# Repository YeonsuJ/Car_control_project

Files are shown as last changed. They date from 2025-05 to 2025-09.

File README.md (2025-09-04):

# 핸들링 모션 기반 RC카 네트워크 시스템 개발
이 리포지토리는 `핸들링 모션 기반 RC카 네트워크 시스템` 프로젝트의 기획부터 최종 구현까지 모든 개발 과정, 소스 코드, 기술 문서를 기록하는 메인 개발 아카이브입니다.

## 프로젝트 문서
프로젝트 개발 과정에서 작성된 모든 문서는 develop 브랜치의 `docs` 폴더 내에 체계적으로 정리되어 있습니다.
```
docs/
├── 3d_model/           # 컨트롤러 외형 설계 도면
├── datasheets/         # 개발에 참고한 부품 데이터시트
├── dev_logs/           # 상세 개발 일지
├── images/             # 프로젝트 관련 사진
├── troubleshooting/    # 문제 해결 과정 기록
├── wiring_diagram/     # 하드웨어 배선도
├── dev_log_summary.md  # 주간 개발 일지 요약
└── parts_list.md       # 전체 부품 목록
```
**주간 개발 일지 요약** : 전체 진행 상황은 [dev_log_summary.md](./docs/dev_log_summary.md) 에서 확인하실 수 있습니다.

---

## 브랜치 전략
기능 단위 개발을 위해 아래와 같이 브랜치를 나누어 관리합니다. 각 브랜치에는 해당 기능의 개발 소스 코드가 커밋 단위로 기록되어 있으며, 상세 개발 히스토리는 별도 문서로 확인할 수 있습니다.

- `main` : 최종 안정화 버전의 코드가 병합되는 기본 브랜치 
- `develop` : 개발 과정에서 작성된 모든 문서를 관리하는 브랜치
- `Unit_controller` : 컨트롤러 유닛 개발 → [[상세 히스토리](https://github.com/YeonsuJ/Car_control_project/tree/Unit_controller/ver_Unit_controller.md)]
- `Unit_car_central` : 차량 메인 제어 유닛 개발 → [[상세 히스토리](https://github.com/YeonsuJ/Car_control_project/tree/Unit_car_central/ver_Unit_car_central.md)]
- `Unit_car_sensor` : 차량 센서 제어 유닛 개발 → [[상세 히스토리](https://github.com/YeonsuJ/Car_control_project/tree/Unit_car_sensor/ver_Unit_car_sensor.md)]
- `Unit_car_status` : 차량 상태 디스플레이 유닛 개발 → [[상세 히스토리](https://github.com/YeonsuJ/Car_control_project/tree/Unit_car_status/ver_Unit_car_status.md)]

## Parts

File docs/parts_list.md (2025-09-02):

# 개발 간 사용한 보드 및 모듈

**Board**
| 품목 | 용도 | 수량 | 이미지 |
| :---: | :---: |:---: |:---: |
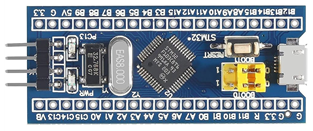
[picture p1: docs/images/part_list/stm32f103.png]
| STM32F103C8T6 | controller MCU <br> car_central ECU <br> car_status ECU <br> car_sensor ECU |4| |
<br/>

**Sensor**
| 품목 | 용도 | 수량 | 이미지 |
| :---: | :---: |:---: |:---: |
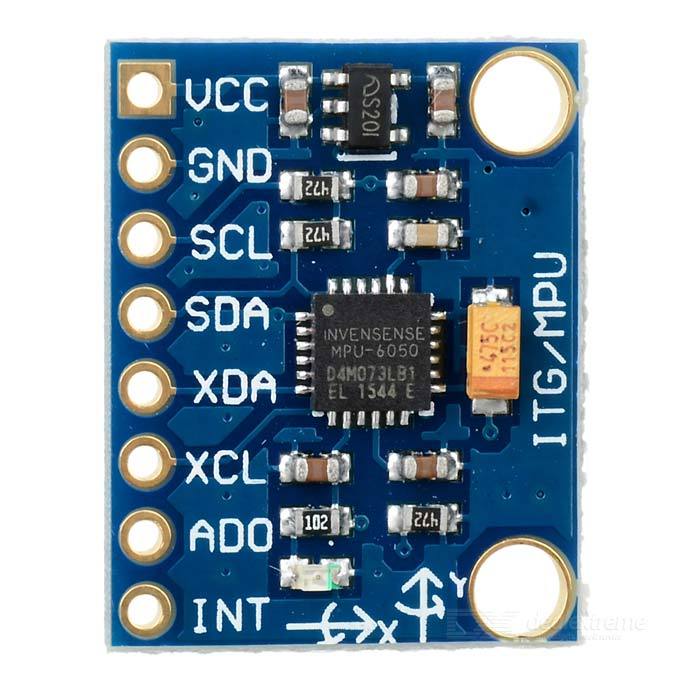
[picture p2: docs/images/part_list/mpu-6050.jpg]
| [MPU-6050] 6축 IMU 센서 | controller - 모션 제어|1||
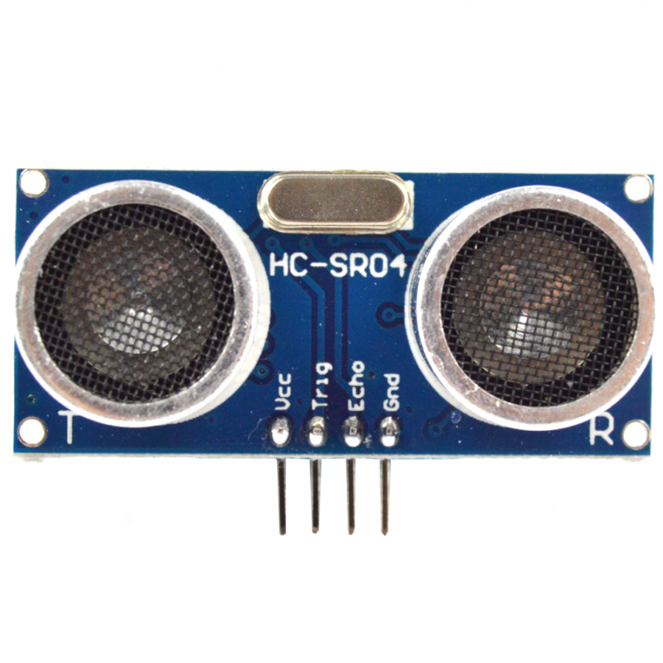
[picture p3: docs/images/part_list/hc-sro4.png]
|[HC-SRO4] 초음파센서|전/후방 장애물 감지|2||
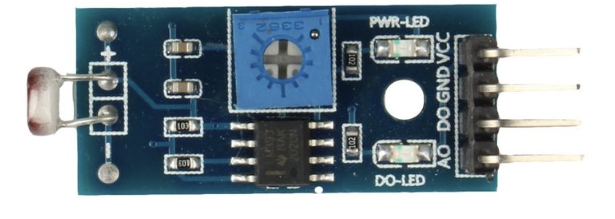
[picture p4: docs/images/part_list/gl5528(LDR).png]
|[LM393 ldr] 조도센서|주변 밝기 판단|1||
<br/>

**Communication module**
| 품목 | 용도 | 수량 | 이미지 |
| :---: | :---: |:---: |:---: |
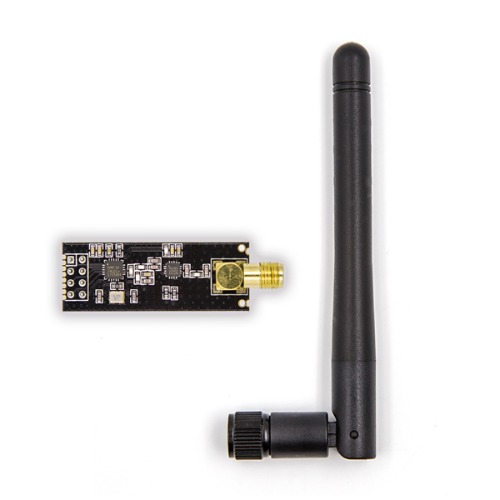
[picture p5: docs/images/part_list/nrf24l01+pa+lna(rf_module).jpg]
|[NRF24L01+PA+LNA] 2.4G 무선 모듈|car-controller RF 통신|2||
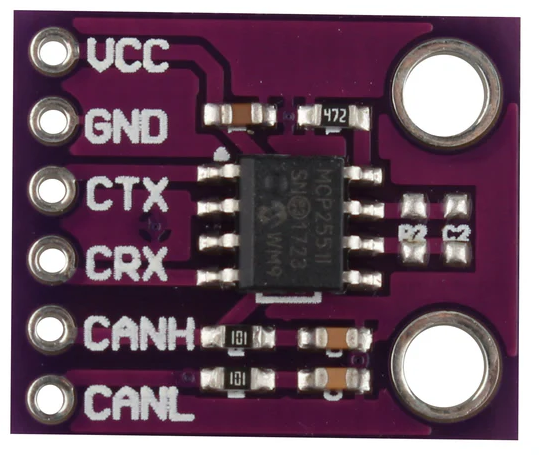
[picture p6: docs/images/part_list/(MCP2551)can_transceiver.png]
|[MCP2551] CAN 트랜시버 모듈| car - can 통신 |3||
<br/>

**Motor**
| 품목 | 용도 | 수량 | 이미지 |
| :---: | :---: |:---: |:---: |
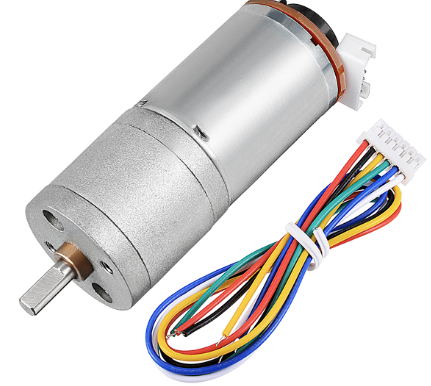
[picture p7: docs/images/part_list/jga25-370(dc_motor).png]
|[JGA25-370] DC모터|내부 인코더를 통해 dc모터의 RPM 확인가능|1||
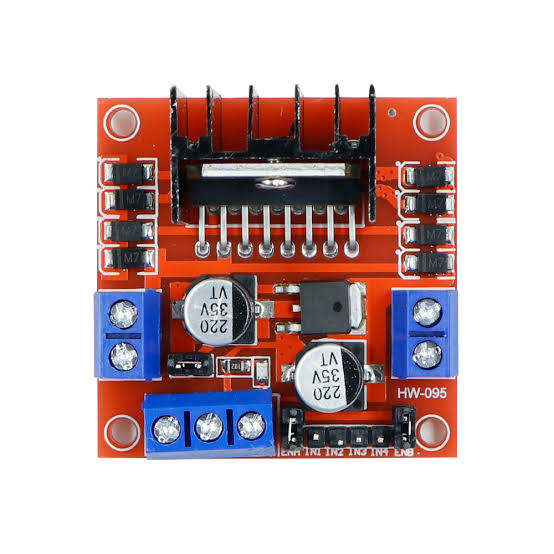
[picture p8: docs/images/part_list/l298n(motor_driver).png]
|L298N|Dc motor driver - DC모터 PWM 제어 및 방향 변경|1||
|진동모터|controller - 충돌 경고 핸들 진동|2|부품 이미지|
|[MG996R]servo 모터|전륜 조향|1|부품 이미지|
<br/>

**Etc**
| 품목 | 용도 | 수량 | 이미지 |
| :---: | :---: |:---: |:---: |
|RC카 섀시, 휠|차량의 뼈대|1|부품 이미지|
|Locker 스위치| car - 배터리 on/off |1|부품 이미지|
|토글 스위치| controller - 기어변속|1|부품 이미지|
|tactile 스위치|브레이크,악셀 버튼용|2|부품 이미지|
|LED|전조등, 후미등, 브레이크등|6|부품 이미지|
|OLED 디스플레이| controller - 주행 중 현황 확인 <br> car - 차량 상태 확인 |2|부품 이미지|
|충전형 18650 리튬 배터리(3000mAh)| car - 3s <br> controller - 2S|5|부품 이미지|
|DC 스텝다운 컨버터| MCU 5V 전압공급 목적 강압 <br> car : 12v->5v <br> controller : 8v->5v |2|부품 이미지|
|저항|120옴 - CAN 종단저항(3) <br> 100옴 - LED용(6)|9|부품 이미지|

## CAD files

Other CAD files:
docs/3d_model/Cap.ipt
docs/3d_model/Steering_Wheel.ipt

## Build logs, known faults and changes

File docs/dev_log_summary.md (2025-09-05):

# Weekly Dev_log Summary 

## 1주차 (25-05-12 ~ 25-05-18) 
|내용|문서 링크|커밋해시|
|---|:---:|:---:|
|- 초기 아이디어 구상<br>- 보드 및 부품 선정 후 구매<br>- 마일드스톤 개괄 작성|[Initial_Planning.md](./dev_logs/Initial_Planning.md)|-|

---

## 2주차 (25-05-19 ~ 25-05-25)
|내용|문서 링크|커밋해시|
|---|:---:|:---:|
|Git commands 학습|[Github_Manuals.md](./dev_logs/Github_Manuals.md)|-|
|Github을 활용한 버전관리법 학습|[Managing_Ver.md](./dev_logs/Managing_Ver.md)|-|
|STM32CubeIDE와 Git & Github 관리/연동|[Managing_Git_CubeIDE.md](./dev_logs/Managing_Git_CubeIDE.md)|-|
|폴링방식 기반 -> 인터럽트 기반 타이머 인풋 캡쳐 활용 초음파센서 거리값 출력 로직 구현 |[Ultrasonic.md](./dev_logs/Ultrasonic.md)|[`7165ee7`](https://github.com/YeonsuJ/Car_control_project/commit/7165ee7f55b6ba93f8e09380047e063f922466cb)|

---

## 3주차 (25-05-26 ~ 25-06-01)
|내용|문서 링크|커밋해시|
|---|:---:|:---:|
|자이로센싱값 -> OLED 모니터링 로직 구현|[Gyro_Display.md](./dev_logs/Gyro_Display.md)|[`229aaa8`](https://github.com/YeonsuJ/Car_control_project/commit/229aaa8b4e313b1294b8de80c3d619d1e4bc61c4)|
|배터리 잔량 측정 -> LCD 모니터링 로직 구현|[Lcd_Battery_Check.md](./dev_logs/Lcd_Battery_Check.md)|[`3cadc21`](https://github.com/YeonsuJ/Car_control_project/commit/3cadc214babbb125b15034e2ebce0408e0c439cd)|
|서보모터 PWM 듀티비 기반 조향 각도 매핑 및 좌/우 조향 한계각 보정|[Servo_Motor.md](./dev_logs/Servo_Motor.md)|[`1d18eda`](https://github.com/YeonsuJ/Car_control_project/commit/1d18eda88c05c9aac707a6153e64591776d5ae05)|
|자이로 roll 값 -> 서보모터 구동|[Gyro_Pwm_Mapping.md](./dev_logs/Gyro_Pwm_Mapping.md)|[`7dc0c12`](https://github.com/YeonsuJ/Car_control_project/commit/7dc0c1298043c86b4969e85140554ca7ac16d90a)|

---

## 4주차 (25-06-02 ~ 25-06-08)
|내용|문서 링크|커밋해시|
|---|:---:|:---:|
|버튼 눌림 시간 측정 로직 구현|[Timer_Switch.md](./dev_logs/Timer_Switch.md)|[`7dcde54`](https://github.com/YeonsuJ/Car_control_project/commit/7dcde5411003d99339164ecea6fa701451369387)|
|PWM 듀티비 기반 DC모터 동작 로직 구현|[Dc_Motor.md](./dev_logs/Dc_Motor.md)|[`45c4e16`](https://github.com/YeonsuJ/Car_control_project/commit/45c4e164ce43241788da8687f2dbf96ccc241a7f)|

---

## 5주차 (25-06-09 ~ 25-06-15)
|내용|문서 링크|커밋해시|
|---|:---:|:---:|
|버튼 누름 시간 기반 DC 모터 속도 제어 및 로커 스위치 전/후진 전환 + OLED 상태 표시 기능 구현|-|[`ad9f4bc`](https://github.com/YeonsuJ/Car_control_project/commit/ad9f4bc341844dbb1dcecefefb23643b87a2f076)|
|초음파센서 거리설정값 기반 진동모터 햅틱 피드백 로직 추가|[Ultrasonic_Vibration.md](./dev_logs/Ultrasonic_Vibration.md)|[`3be3675`](https://github.com/YeonsuJ/Car_control_project/commit/3be3675e9acbf0c19c06f436050e4edda30a9942)|

---

## 6주차 (25-06-16 ~ 25-06-22)
|내용|문서 링크|커밋해시|
|---|:---:|:---:|
|선형 보간 방식 기반 ADC 배터리 측정 후 OLED 출력 로직으로 수정|[Adc_Oled_Battery_Check.md](./dev_logs/Adc_Oled_Battery_Check.md)|[`7bd584e`](https://github.com/YeonsuJ/Car_control_project/commit/7bd584ef51410f1fcd1aae941d038a377702ed81)|
|핸들 디자인·3D 모델링 및 출력|[Controller_3D_Modeling_Log.md](./dev_logs/Controller_3D_Modeling_Log.md)|모델링 파일 : [Cap.ipt](../3d_model/Cap.ipt) / [Steering_Wheel.ipt](../3d_model/Steering_Wheel.ipt)|

---

## 7주차 (25-06-23 ~ 25-06-29)
|내용|문서 링크|커밋해시|
|---|:---:|:---:|
|DC모터와 Servo모터 동작 기능 통합 및 핀 라벨링 추가|-|[`b474df6`](https://github.com/YeonsuJ/Car_control_project/commit/b474df67b9a24d75a08725cf00dbaa94170cabac)|
|RF 통신을 통한 roll 값, 악셀 / 브레이크 버튼 눌림 시간 송수신 및 실시간 서보모터 조향 구현 (m3)|[M3_RF_Communication.md](./dev_logs/M3_RF_Communication.md)|[`RX`](https://github.com/YeonsuJ/Car_control_project/commit/cbc18035c71e6f3c50977fd6d9abb157786e36d2) / [`TX`](https://github.com/YeonsuJ/Car_control_project/commit/88aaa169f57b4323f77507a8af936f329d8cdfcc)|

---

## 8주차 (25-06-30 ~ 25-07-06)
|내용|문서 링크|커밋해시|
|---|:---:|:---:|
|CAN 통신 송/수신 초기 기능 구현 (m3)|[Can_Communication.md](./dev_logs/Can_Communication.md)|[`RX`](https://github.com/YeonsuJ/Car_control_project/commit/89800bed5bbd43df382bfc1d63d63a506a9933f4) / [`TX`](https://github.com/YeonsuJ/Car_control_project/commit/e1316b007e2b4ca462092e7ce0a50db136938af6)|
|M3보드 기반 RF 송/수신 모터 제어 통합 (v1.0.0)|[V1.0.0_RF_MotorCtrl.md](./dev_logs/V1.0.0_RF_MotorCtrl.md)|[`central_v1.0.0`](https://github.com/YeonsuJ/Car_control_project/commit/087c00a452b5e8d1e8889b24831789548ee6a3f0) / [`controller_v1.0.0`](https://github.com/YeonsuJ/Car_control_project/commit/de77deb8e3d7acceab46b517a5e457805b62f0cb)|

---

## 9주차 (25-07-07 ~ 25-07-13)
|내용|문서 링크|커밋해시|
|---|:---:|:---:|
|코드 리팩토링 및 Locker 스위치 기반 전/후진 기능 추가, <br>DC모터 Encoder 기반 RPM 측정 로직 추가 (v1.1.0)|[V1.1.0_Locker_Encoder.md](./dev_logs/V1.1.0_Locker_Encoder.md)|[`central_v1.1.0`](https://github.com/YeonsuJ/Car_control_project/commit/94a4a332562ac80192bba8cc971c298cab48cbfd) / [`controller_v1.1.0`](https://github.com/YeonsuJ/Car_control_project/commit/241c4c5877d608a3723825619a0ed84717d12e22)|
|컨트롤러부 Lokcer -> 토글스위치 기반 전/후진 기어변속 수정 및 센서부 엔코더 기반 RPM 측정 로직 수정|[RPM_Measuring_Dir_Toggle.md](./dev_logs/RPM_Measuring_Dir_Toggle.md)|-|

---

## 10주차 (25-07-14 ~ 25-07-20)
|내용|문서 링크|커밋해시|
|---|:---:|:---:|
|ACK 페이로드 기반 RF 양방향 송수신 구현(v1.5.0)|[V1.5.0_ACK_Payload.md](./dev_logs/V1.5.0_ACK_Payload.md)|[`controller_v1.5.0`](https://github.com/YeonsuJ/Car_control_project/commit/0745e3354e6c7a4ae12c31953c2b0a166a373d1a) / [`central_v1.5.0`](https://github.com/YeonsuJ/Car_control_project/commit/fb063337c0dd13055ecf7afc8d4cca3d3b347613)|
|Broadcast 기반 CAN 송/수신 초음파센서 -> 햅틱센서 제어 통합(v1.5.0)|[V1.5.0_Broadcast_Can_Comm.md](./dev_logs/V1.5.0_Broadcast_Can_Comm.md)|[`central_v1.5.0`](https://github.com/YeonsuJ/Car_control_project/commit/fb063337c0dd13055ecf7afc8d4cca3d3b347613) / [`sensor_v1.5.0`](https://github.com/YeonsuJ/Car_control_project/commit/13f38c18cb6364108f1dbb893375f56113965320) / [`status_v1.5.0`](https://github.com/YeonsuJ/Car_control_project/commit/d7810ab06a289a489a91285c02ddfea00daa1e14)|

---

## 11주차 (25-07-21 ~ 25-07-27)
|내용|문서 링크|커밋해시|
|---|:---:|:---:|
|Controller 부 파일 분할 및 코드 최적화|[V1.6.0_Controller_Refactor.md](./dev_logs/V1.6.0_Controller_Refactor.md)|[`controller_v1.6.0`](https://github.com/YeonsuJ/Car_control_project/commit/033420c3bb7774f772402cf7f1a2d00c62ac3682)|
|Central 부 파일 분할 및 코드 최적화 + CAN 개선|[V1.6.0_Central_Refactor.md](./dev_logs/V1.6.0_Central_Refactor.md)|[`central_v1.6.0`](https://github.com/YeonsuJ/Car_control_project/commit/f1f14c615f58d526c636ad07ba73be2855ed3e86)|
|Sensor 부 파일 분할 및 코드 최적화 + CAN 개선|[V1.6.0_Sensor_Refactor.md](./dev_logs/V1.6.0_Sensor_Refactor.md)|[`sensor_v1.6.0`](https://github.com/YeonsuJ/Car_control_project/commit/22e10d68004d4dc19ce922d08332d6f769065621)|
|Status 부 파일 분할 및 코드 최적화 + CAN 개선, ADC 배터리 측정 추가|[V1.6.0_Status_Refactor.md](./dev_logs/V1.6.0_Status_Refactor.md)|[`status_v1.6.0`](https://github.com/YeonsuJ/Car_control_project/commit/ff784f4d59c5a10102964285e873eb8930eb3fa3)|

---

## 12주차 (25-07-28 ~ 25-08-03)
|내용|문서 링크|커밋해시|
|---|:---:|:---:|
|LDR 기반 전/후진 및 브레이크 상태에 따라 전조등·후미등 제어 로직 추가|[V1.7.0_LDR_Brk_Dir_LED_Ctrl.md](./dev_logs/V1.7.0_LDR_Brk_Dir_LED_Ctrl.md)|[`central_v1.7.0`](https://github.com/YeonsuJ/Car_control_project/commit/c3081ab3b98114f977e82bb3962f7fc1301cce8b) / [`sensor_v1.7.0`](https://github.com/YeonsuJ/Car_control_project/commit/2e1ab4625bc36b59d184030a2293edb108fda21f) / [`status_v1.7.0`](https://github.com/YeonsuJ/Car_control_project/commit/e6da3eca9ead389a608fc11dc43a8671dc7fec93) |
|Controller부 RTOS 포팅 완료|[V2.0.0_Controller_Porting_RTOS.md](./dev_logs/V2.0.0_Controller_Porting_RTOS.md)|[`controller_v2.0.0`](https://github.com/YeonsuJ/Car_control_project/commit/48f5d81bfadd766953063530f16cc98a43dc841b)|

---

## 13주차 (25-08-04 ~ 25-08-10)
|내용|문서 링크|커밋해시|
|---|:---:|:---:|
|central부 RTOS 포팅 및 코드 리팩토링 완료|[V2.0.0_Central_Porting_RTOS.md](./dev_logs/V2.0.0_Central_Porting_RTOS.md)|[`central_v2.0.0`](https://github.com/YeonsuJ/Car_control_project/commit/785f3c91b83969a0039c02a31b324fe7f5a3fb35)|
|Sensor부 RTOS 포팅 및 코드 리팩토링 완료|[V2.0.0_Sensor_Porting_RTOS.md](./dev_logs/V2.0.0_Sensor_Porting_RTOS.md)|[`sensor_v2.0.0`](https://github.com/YeonsuJ/Car_control_project/commit/0badf8a49d77cd7876f95e2272191a7e3ae24f67)|
|Status부 RTOS 포팅 및 코드 리팩토링 완료|[V2.0.0_Status_Porting_RTOS.md](./dev_logs/V2.0.0_Status_Porting_RTOS.md)|[`status_v2.0.0`](https://github.com/YeonsuJ/Car_control_project/commit/bf95e1d0ea4555b5037cee12cbdc72679ce1b4e9)|

---

## 14주차 (25-08-11 ~ 25-08-17)
|내용|문서 링크|커밋해시|
|---|:---:|:---:|
|컨트롤러부 디스플레이 태스크 및 전/후진, RPM OLED 출력 로직 추가 (v2.1.0)|[V2.1.0_Add_DisplayTask_RPM_DR.md](./dev_logs/V2.1.0_Add_DisplayTask_RPM_DR.md)|[`controller_v2.1.0`](https://github.com/YeonsuJ/Car_control_project/commit/09c66b3d7516d6cdac1aea90c0a5b4c18c4fe034)|
|차량부 부품 재배치 및 회로, 케이블 정리|-|-|
|컨트롤러부 최종 코드 리팩토링 완료 (v2.2.0)|-|[`controller_v2.2.0`](https://github.com/YeonsuJ/Car_control_project/commit/d0602d02236190beffc51e91d928c0040a883730)|

---

## 15주차 (25-08-18 ~ 25-08-24)
|내용|문서 링크|커밋해시|
|---|:---:|:---:|
|Github 저장소 및 개발일지 최종 정리|-|-|
|시연영상 촬영 및 편집|-|-|

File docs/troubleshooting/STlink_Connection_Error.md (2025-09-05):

# ST-LINK 연결 문제 해결

---

## 문제 상황 (Problem)

1.  **`fail.txt` 파일에 아래와 같은 오류 메시지 발생:**
    ```
    The interface firmware FAILED to reset/halt the target MCU
    ```

2.  **ST-LINK Utility에서 `Target > Connect` 시도 시 에러 발생:**
    ```
    Can not connect to target!
    ```

3.  **전원 LED는 정상적으로 점등됨** (하드웨어 쇼트는 아닌 것으로 추정).

> 위와 같은 문제는 칩에 프로그래밍된 코드가 ST-LINK의 디버깅 인터페이스(SWD/JTAG) 핀을 다른 용도로 사용하거나, 칩을 저전력 모드로 즉시 전환시켜 연결을 방해할 때 주로 발생한다.

---

## 해결법 (Solution): BOOT0 핀을 이용한 부트로더 모드 진입

MCU가 사용자의 코드를 실행하지 않고 내장된 시스템 부트로더로 바로 진입하도록 하여, ST-LINK가 안정적으로 연결될 수 있는 환경을 만들어 준다.

### 단계별 절차

1.  **전원 완전 분리**
    * 보드에 연결된 ST-LINK와 전원 케이블을 모두 제거한다.

2.  **BOOT0 핀 설정 변경**
    * 보드에 있는 **BOOT0 핀을 3.3V(VDD)에 연결**한다. (점퍼를 옮기거나, 와이어를 이용해 직접 연결)
    * **BOOT1 핀은 0V(GND)에 연결**된 상태를 유지한다.

3.  **전원 재연결**
    * BOOT0 핀이 3.3V에 연결된 상태에서 보드에 전원을 다시 인가한다.
    * 이제 MCU는 사용자가 작성한 코드가 아닌 내장된 시스템 부트로더로 실행된다.

4.  **ST-LINK Utility 연결**
    * ST-LINK Utility를 실행하고 `Target > Connect`를 클릭한다.
    * 정상적으로 연결되면 칩의 정보가 표시된다.

5.  **칩 전체 메모리 삭제**
    * 연결 성공 후, 상단 메뉴에서 `Target > Erase Chip`을 선택하여 칩의 전체 내용을 삭제한다.
    * "Erase memory performed successfully" 메시지를 확인한다.

6.  **원상 복구**
    * 작업이 완료되면 보드 전원을 다시 분리한다.
    * **BOOT0 핀을 원래 상태(GND에 연결)로 되돌려 놓는다.**

    * 이제 다시 전원을 연결하고 정상적으로 펌웨어를 다운로드하거나 디버깅을 시작할 수 있다.

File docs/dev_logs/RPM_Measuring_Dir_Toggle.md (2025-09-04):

# Sensor부 Encoder 기반 RPM 측정 및 Controller부 토글스위치 기반 전/후진 기어변속 구현

## 프로젝트 활용 방안
- Sensor ECU: DC 모터의 회전 속도를 정밀하게 측정하여 차량의 속도 데이터로 활용 이를 추후에 컨트롤러에 디스플레이
- Controller : 사용자의 토글 스위치 입력을 받아 차량의 주행 방향(전진/후진)을 결정하고, 이를 무선 통신으로 차량에 명령
---

## 이론 개요

- 엔코더(Encoder) 기반 RPM 측정
    - STM32의 타이머(TIM)는 하드웨어 Quadrature Encoder Mode를 지원하여, 모터의 속도와 회전 방향을 최소한의 CPU 부하로 정밀하게 측정할 수 있다.
    - 엔코더의 A상과 B상 신호를 모두 사용하면 두 채널 간 위상 차이를 통해 회전 방향을 감지할 수 있으며, 각 펄스의 상승/하강 엣지를 모두 카운트하여 최대 4배의 분해능으로 정밀한 측정이 가능하다.

    > [자세한 엔코더 설명(Dc_Motor.md) 참고](./Dc_Motor.md)

- 토글 스위치로 전/후진 기어변속 구현
    - 3핀 토글 스위치는 가운데 공통(COM) 핀과 양쪽 단자를 가져, 한쪽은 전진(Forward), 다른 쪽은 후진(Backward) 신호 입력에 적합하다.
    - 스위치는 상태가 한번 결정되면 기계적으로 고정되는 특성이 있고 접점 노이즈가 거의 없어, 10~20ms 주기로 상태를 주기적으로 확인하는 폴링(Polling) 방식이 인터럽트 방식보다 안정적이고 구현이 간단하다.

---

## 하드웨어 연결
- 센서부 Encoder 연결도<br>
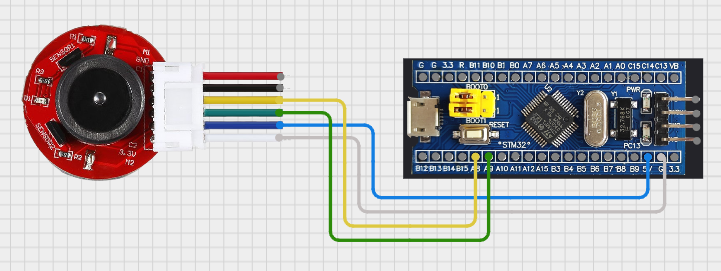
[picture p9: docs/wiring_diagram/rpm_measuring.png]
RPM 측정 배선도
    
- 컨트롤러부 토글스위치 연결도<br>
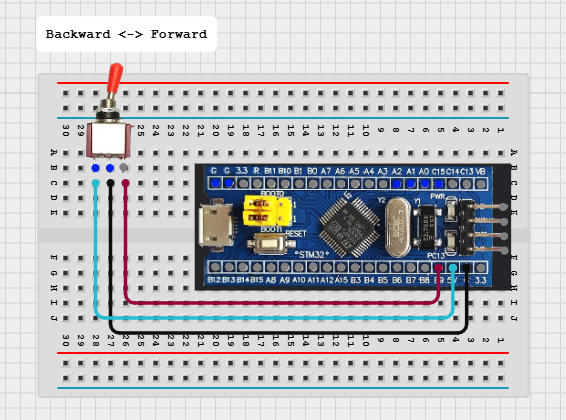
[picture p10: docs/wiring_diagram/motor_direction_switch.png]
토글스위치 모터방향 제어 배선도
    

### Sensor
- Encoder +5v (blue)
- Encoder Gnd(black)
- Encoder Signal A (yellow) : PA8 (TIM1_CH1)
encoder signal B(green) : PA9 (TIM1_CH2)

### Controller
- PB9(Motor_Forward) : GPIO_Input
- PB8(Motor_Backward) : GPIO_Input
- Middle Pin : GND

---

## STM32CubeMX 설정

### Sensor
Sensor ECU: TIM1 설정 - Encoder Mode
- Combined Channels: Encoder Mode
- Configuration > Parameter Settings
    - Encoder Mode: Encoder Mode TI1 and TI2 (A상, B상 모두 사용)
- Counter Settings
    - Prescaler: 0 (입력 클럭을 분주 없이 그대로 사용)
    - Counter Period (ARR): 65535 (0xFFFF, 16비트 타이머의 최댓값으로 오버플로우 방지)
Encoder Input Configuration
    - IC1 / IC2 Polarity: Rising Edge
    - IC1 / IC2 Filter: 10 (안정적인 신호 감지를 위해 디지털 필터 적용)

#### IC1/IC2의 Input Filter란?
엔코더 신호에 포함된 전기적 노이즈로 인한 잘못된 펄스 감지를 방지하는 디지털 필터 기능이다. 고속 회전이나 긴 배선으로 노이즈가 유입되면 RPM 값이 튀거나 제어가 불안정해질 수 있는데, 필터 값을 높이면 노이즈 제거에 효과적이다. (0~15 설정 가능)

### Controller
- B8, PB9 핀 설정
    - Mode: Input
    - Pull-up/Pull-down: Pull-up (스위치가 연결되지 않았을 때 기본 상태를 HIGH로 유지)

---
## 코드 설명

### Sensor부: RPM 측정 동작 요약
motor_encoder.c의 Update_Motor_RPM() 함수는 아래와 같은 로직으로 주기적으로 호출되어 RPM을 계산하고 필터링한다. 

```c
// Sensor부 motor_encoder.c의 RPM 측정 핵심 로직
void Update_Motor_RPM(void)
{
    // 1. 이전 값과 현재 값 저장
    static int16_t last_encoder_count = 0;
    static uint32_t last_cycle_count = 0;

    // 2. 현재 엔코더 카운트 및 DWT 사이클 카운트 읽기
    uint32_t current_cycle_count = DWT->CYCCNT;
    int16_t current_encoder_count = (int16_t)__HAL_TIM_GET_COUNTER(&htim1);

    // 3. 변화량 계산
    uint32_t delta_cycles = current_cycle_count - last_cycle_count;
    int16_t delta_encoder = current_encoder_count - last_encoder_count;

    // 4. 다음 측정을 위해 현재 값 저장
    last_encoder_count = current_encoder_count;
    last_cycle_count = current_cycle_count;

    // 5. 경과 시간(초) 및 PPS(Pulse Per Second) 계산
    float delta_time_s = (float)delta_cycles / (float)SystemCoreClock;
    float pps = (float)delta_encoder / delta_time_s;

    // 6. RPM 계산 (TICKS_PER_REV: 기어비 등이 반영된 1회전당 총 틱 수)
    float raw_rpm = (pps / TICKS_PER_REV) * 60.0f;

    // 7. 저주파 통과 필터(IIR)를 적용하여 값을 부드럽게 처리
    filtered_rpm = (RPM_FILTER_ALPHA * raw_rpm) + ((1.0f - RPM_FILTER_ALPHA) * filtered_rpm);
    motor_rpm = filtered_rpm;
}
```

### Controller부: 토글스위치 기반 방향 전환 작동 원리

|토글스위치 위치|PB9 상태|PB8 상태|IN1 (central PA0)|IN2 (central PA1)|모터 회전 방향|
|---|----|---|---|---|---|
|전진 (FWD)|LOW|HIGH|0 (LOW)|1 (HIGH)|정방향 회전|
|후진 (REV)|HIGH|LOW|1 (HIGH)|0 (LOW)|역방향 회전|

- 토글 스위치는 한 번 누르면 한 쪽으로 고정되어 LOW 상태가 지속되므로 폴링 방식이 적절함
- 둘 다 HIGH일 경우, 방향은 변경되지 않고 직전 설정 상태 유지된다.

#### 동작 원리:

1. PB9 핀의 상태를 읽는다. (HIGH/LOW)
2. 스위치가 전진(FWD) 위치에 있으면 PB9는 GND와 연결되어 LOW 상태가 되고, 함수는 LOCKER_FORWARD를 반환한다.
3. 스위치가 후진(REV) 위치에 있으면 PB9는 내부 풀업 저항에 의해 HIGH 상태가 되고, 함수는 LOCKER_BACKWARD를 반환한다.

---

## 개선사항 

### CubeMX에서 Peripheral 별 파일 분할

#### 설정 방법
1. CubeMX 실행 후 .ioc 파일 열기
2. 상단 메뉴에서<br>
    Project Manager > Code Generator 탭 선택
3. Generate peripheral initialization as a pair of '.c/.h' files per peripheral   
4. 저장 후 GENERATE CODE 클릭

- 이 설정이 되어 있지 않으면 main.c 내부나 stm32f4xx_hal_msp.c 등에 모든 초기화 코드가 모이게 된다.

#### Peripheral 별 파일 분할의 장점
- 가독성 향상
    - 각 주변장치의 설정이 해당 전용 파일에 명확히 구분되므로, 코드를 파악하고 수정하기 쉬워짐
- 유지보수 용이
    - 예를 들어 I2C 설정만 바꾸고 싶을 때 i2c.c만 보면 되며, 다른 설정과 충돌하지 않도록 관리가 용이함
- 빌드 속도 개선
    - 변경이 발생한 .c 파일만 컴파일되므로, 프로젝트 규모가 클수록 빌드 시간 감소에 효과적임
- Git 버전관리 효율 
    - 기능별로 커밋이 가능하므로 이력 관리가 체계적으로 됨. (예: tim.c만 수정한 경우 diff 확인이 쉬움)
- 팀 협업에 유리
    - 여러 사람이 동시에 I2C, TIM 등 서로 다른 기능을 작업할 수 있어 충돌 가능성이 줄어들게 됨

--- 

## 향후 확장 및 개선 아이디어

- Sensor ECU: 현재 RPM 측정에 사용된 저주파 통과 필터의 계수(RPM_FILTER_ALPHA)를 주행 환경에 따라 동적으로 조절하여 반응성과 안정성 사이의 균형을 최적화하는 방안을 연구할 수 있다.

- Controller ECU: 현재 폴링 방식으로 처리되는 스위치 입력을, 상태 변경 시에만 이벤트가 발생하는 외부 인터럽트(EXTI) 방식으로 변경하여 CPU 점유율을 최소화하는 리팩토링을 고려할 수 있다. (단, 디바운싱(Debouncing) 로직 추가 필요)

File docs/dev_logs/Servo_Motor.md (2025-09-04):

# [MG996R] 서보모터 동작 로직 구현

## 프로젝트 활용 방안
본 프로젝트에서 서보모터는 차량의 전륜 조향을 담당하며, 핸들에 부착된 자이로센서의 실시간 센싱 데이터를 기반으로 조향 각도를 제어한다.

---

## 이론 개요

### MG996R 서보모터와 PWM 동작원리
- 서보모터는 PWM(Pulse Width Modulation) 신호를 통해 제어되며, 이 신호는 일정한 주기(보통 20ms, 즉 50Hz)를 가지는 펄스 형태이다.
이때 펄스의 High 상태(ON 시간), 즉 펄스 폭(Pulse Width)에 따라 모터의 회전 각도가 결정된다.
- 서보모터 동작에서 듀티비(Duty Cycle)는 전체 주기 중 High 상태가 차지하는 비율을 의미하며, 이 듀티비(또는 펄스 폭)가 서보의 위치를 결정한다.
- MG996R과 같은 서보모터의 경우 일부 제품은 0.5ms ~ 2.5ms까지도 지원하지만, 안정적인 동작을 위해 일반적으로 1.0ms ~ 2.0ms 범위의 펄스 폭에 따라 약 -90° ~ +90° 사이의 각도로 회전한다.

> [MG996R datasheet](../datasheets/MG996R_datasheet.pdf)<br>
> 참고링크 : https://www.youtube.com/watch?v=HN9sKhKxy7M
---

## 하드웨어 연결

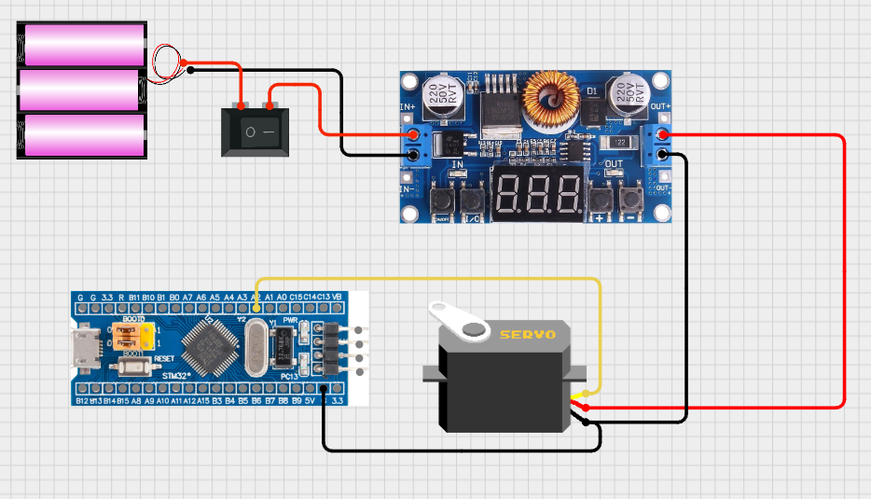
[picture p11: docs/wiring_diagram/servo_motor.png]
서보모터 결선도


<br>
MG996R 서보모터는 안정적인 동작을 위해 4.8V~7.2V의 전압이 요구된다. 그러나 STM32 보드의 5V 핀은 전류 공급 능력이 500mA 이하로 제한되어 있어, 부하가 걸릴 경우 순간적으로 최대 2.5A까지 전류를 요구하는 MG996R에 충분한 전력을 공급하기 어렵다. 이에 따라, VCC와 GND는 배터리에서 스텝다운 컨버터를 통해 5V로 강압한 외부 전원에 연결하여 안정적인 전원 공급이 가능하도록 구성하였다.

<br><br>
### 연결
|MG996R|외부 전원|F103 보드|
|:---:|:---:|:---:|
|Vcc|+5V|-|
||공통 Gnd||
|PWM|-|PA2|

---  

## STM32CubeMX 설정
Click Timer → Click TIM2 →
- Channel3 set to PWM Generation CH3
Configuration → Parameter Settings →
- Prescaler set to 72-1
- Counter Period : 19999

### 1. PWM 주기 계산
- 서보모터가 요구하는 PWM 주기인 20ms(50Hz)를 맞추기 위해 타이머 클럭과 Prescaler, Counter Period의 값을 조합하여 계산하며, 공식은 다음과 같다.<br>

```latex
PWM 주기 (T) = ((Counter Period + 1) × (Prescaler + 1)) / Timer Clock(Hz)
```

#### 타이머 클럭(Hz) 계산
- STM32F103C8T6의 시스템 클럭은 일반적으로 72MHz로 설정된다.
- TIM2는 APB1 버스에 연결되어 있으며, APB1 Prescaler가 1보다 클 경우 타이머 클럭은 APB1 클럭의 2배가 된다. (APB1 클럭 36MHz * 2 = 72MHz)
- 결과적으로 TIM2에 공급되는 최종 클럭은 72MHz가 된다.

#### PWM 주기 계산 적용
위 설정값과 클럭을 공식에 대입하면 다음과 같다.

```latex
PWM 주기 (초) = ((19999 + 1) × (71 + 1)) / 72,000,000 Hz
             = (20000 × 72) / 72,000,000
             = 1,440,000 / 72,000,000 = 0.02초 = 20ms
```

### 2. PWM 주파수 계산
```latex
주파수(f) = 1 / 주기(T) = 1 / 0.02s = 50Hz
```

### 3. 펄스 폭(Pulse Width) 계산
펄스 폭(Pulse Width)은 PWM 신호에서 High 상태가 유지되는 시간을 의미하며, 이는 타이머의 설정 값(Prescaler, Period, Compare Value)에 따라 결정된다. PWM 출력에서 __HAL_TIM_SET_COMPARE() 함수로 설정하는 값은 타이머 카운트 기준의 Compare Match 값으로, 곧 High 상태가 유지되는 시간(카운트 수)을 나타낸다.

PWM 신호의 High 구간 길이는 __HAL_TIM_SET_COMPARE() 함수로 설정하는 Compare 값에 의해 결정된다. 타이머가 1카운트 하는 데 걸리는 시간(Tick 시간)은 다음과 같다.

```latex
Tick 시간 = (PSC + 1) / 타이머 클럭 = 72 / 72,000,000Hz = 1µs
```

따라서 최종 펄스 폭은 Compare 값과 같다.

```latex
펄스 폭(µs) = Compare 값 × 1µs
```

### 4. 듀티비(Duty Cycle) 계산
듀티비란, PWM(펄스 폭 변조, Pulse Width Modulation) 신호에서 하나의 주기 동안 신호가 High 상태로 유지되는 비율을 뜻하며, 백분율(%)로 다음과 같이 계산한다.

```latex
듀티 비(%) = High 상태 시간 / 전체 주기 시간 × 100
```

- 듀티비가 높다 -> High 상태가 더 길다 -> 서보가 더 많이 회전
- 듀티비가 낮다 -> High 상태가 짧다 -> 덜 회전

※ STM32 같은 MCU에서는 TIMx->CCR 레지스터로 이 듀티비를 설정한다.

<br>
서보모터는 듀티비 자체보다는 펄스 폭(ms)을 해석하지만, 주기가 20ms로 고정된 상태에서는 펄스 폭과 듀티비가 직접 연결된다.<br>
ex) 1.5ms Pulse = 20ms 주기 -> 7.5% Duty Cycle

---
#### 서보모터 PWM 듀티비 기반 조향 각도 매핑 구현 및 좌/우 조향 한계각 보정

## 코드 설명
동작 요약 : 차량 섀시의 하드웨어 형태에 맞게 설정한 조향 한계값 범위 내에서 Compare 값(펄스 폭)을 변경하여 중립, 우회전, 좌회전 순서로 조향을 반복한다. 

### main 함수 동작 요약
```c
HAL_TIM_PWM_Start(&htim2, TIM_CHANNEL_3);  // TIM2 채널 3(PA2)에서 PWM 시작
```

```c
while (1)
{
  __HAL_TIM_SET_COMPARE(&htim2, TIM_CHANNEL_3, 1200); // 우회전 최대 (roll -90°): Compare = 1200 → 1.2ms 펄스 폭
  HAL_Delay(1000);
  
  __HAL_TIM_SET_COMPARE(&htim2, TIM_CHANNEL_3, 1900); // 좌회전 최대 (roll +90°): Compare = 1900 → 1.9ms 펄스 폭
  HAL_Delay(1000);
}
```

- 차량 섀시에 닿지 않는 좌우 한계각 범위 내에서 서보모터를 제어하기 위해, Compare 값에 따른 펄스 폭을 계산한다. 
- Tick 시간이 1µs이므로 Compare 값 1200은 1.2ms, 1900은 1.9ms의 펄스 폭에 해당하며, 이 범위를 실제 조향의 좌/우 최대 한계로 설정한다.
- while 루프는 중립 위치 없이, 설정된 최대 우회전(Compare: 1200)과 최대 좌회전(Compare: 1900) 위치를 1초마다 반복적으로 직접 전환하도록 구성한다.

> 참고링크<br>
: https://www.micropeta.com/video102<br>
: https://m.blog.naver.com/compass1111/221163124212<br>
: https://m.blog.naver.com/emperonics/221725399383<br>

---

## 문제 해결 및 개선/확장

### 문제상황 1.
전원을 공급할 때마다 배터리를 홀더에서 탈부착해야 하는 번거로움이 있었다.  <br>
**해결** : 회로의 기준점(Gnd)을 항상 유지하면서 전체 회로에 안전하게 전원을 차단할 수 있도록 + 쪽의 전선 중간에 로커 스위치(정격 3A 250V AC)를 추가하였다. 

---

## 향후 확장 및 개선 아이디어
- 자이로센싱 값 기반 서보모터 조향 로직 통합
- 오실로스코프 PWM 파형 시각화

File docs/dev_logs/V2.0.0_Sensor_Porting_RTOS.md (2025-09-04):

# Sensor ECU, RTOS 포팅 및 시스템 구조 변경 (V2.0.0)

**RTOS 도입의 필요성: 실시간 데이터 수집과 안정적인 전송 보장**

기존의 순차적 `while`(1) 루프 구조는 정밀한 주기로 센서 데이터를 수집하는 동시에, 수집된 데이터를 가공하여 CAN 버스로 전송하는 두 가지 주요 작업을 안정적으로 수행하는 데 한계가 있었다. 특히, RPM 계산과 같이 시간에 민감한 데이터 수집 작업이 CAN 전송 로직에 의해 지연(Jitter)되거나, 반대로 데이터 전송 중 다음 센싱 주기를 놓치는 문제가 발생할 수 있어 데이터의 신뢰성을 보장하기 어려웠다.

본 Sensor 부는 차량의 물리적 상태를 감지하는 실시간 데이터 취득 허브로서, 모든 측정은 예측 가능한 시간 내에 이루어져야 한다. 여러 센서의 독립적인 동작을 보장하고 데이터 수집과 전송 작업을 분리하여 시스템의 실시간성과 안정성을 확보하기 위해 FreeRTOS를 도입, 멀티태스킹 시스템으로 전환했다.

## main.c : RTOS 도입에 따른 구조적 변화

FreeRTOS가 적용되면서 main.c는 어플리케이션의 메인 루프가 아닌, 시스템을 부팅하고 RTOS 스케줄러에 제어권을 넘기는 **시스템 로더(Loader)**로 역할이 변경되었다.

1. main() 함수의 역할 축소

- 초기화 전담: main() 함수는 하드웨어(HAL_Init, MX_..._Init), 커스텀 모듈(DWT_Init), RTOS 커널(osKernelInitialize)을 순서대로 초기화한다.

- 스케줄러 시작: osKernelStart() 함수를 호출하여 모든 제어권을 FreeRTOS 스케줄러로 넘긴다. 이 시점 이후 main()의 while(1) 루프는 더 이상 실행되지 않는 **데드 코드(Dead Code)**가 된다.

2. 데이터 흐름 변경: 순차 처리에서 Message Queue 기반으로

- 기존 방식 (결합 구조): 단일 루프 안에서 센서 값을 읽고, 가공하고, 전송하는 모든 작업이 순차적으로 묶여 있어 한 작업의 지연이 다른 작업에 직접적인 영향을 미치는 구조였다.

- RTOS 방식 (분리 구조): SensorTask가 수집한 데이터를 **메시지 큐(CANTxQueueHandle)**에 삽입하면, 데이터 전송을 기다리며 잠들어 있던 CANTask가 즉시 깨어나 독립적으로 전송을 처리한다. 이로써 데이터 수집과 전송이 완벽히 분리되어, SensorTask는 다른 작업에 방해받지 않고 정밀한 주기를 유지할 수 있다.

3. 어플리케이션 로직의 완전한 태스크 분리

- 기존 main()에 혼재되어 있던 모든 로직(초음파 트리거, RPM 계산, 데이터 패키징, CAN 전송)은 이제 SensorTask와 CANTask라는 독립된 RTOS 태스크로 완전히 분리 및 이관되었다.

## freertos.c : 멀티태스킹 시스템의 구현

freertos.c는 Sensor 보드의 핵심 로직을 담고 있다. 각 기능은 독립적인 **태스크(Task)**로 분리되어 실시간 데이터 처리 능력과 시스템 안정성을 확보한다.

1. RTOS 객체 생성 (MX_FREERTOS_Init)

- 태스크 (Threads)

    - SensorTask (높은 우선순위): 10ms의 정밀한 주기로 초음파, 엔코더 등 모든 센서 데이터를 수집하고 1차 가공하는 핵심 데이터 생산 태스크.

    - CANTask (보통 우선순위): SensorTask가 전달한 데이터를 최종적으로 CAN 프로토콜에 맞게 가공하여 외부로 전송하는 데이터 소비자 태스크.

- 메시지 큐 (Message Queues)

    - CANTxQueueHandle: SensorTask가 생산한 종합 센서 데이터를 CANTask로 안전하게 전달하는 단방향 통신 채널. 데이터 생산 로직과 소비(전송) 로직을 완벽히 분리(Decoupling)한다.

2. 태스크 우선순위 설계

- SensorTask (High Priority): 센서 데이터는 정해진 시간(10ms)에 정확하게 수집되어야 그 값이 유효하다. 데이터 품질을 최우선으로 보장하기 위해 다른 작업에 의해 실행이 방해받지 않도록 가장 높은 우선순위를 부여했다.

- CANTask (Normal Priority): 데이터 전송은 수집된 이후에만 의미가 있으며, 약간의 전송 지연은 시스템 전체에 큰 영향을 주지 않으므로 보통 우선순위로 설정했다.

3. 태스크 구현

- StartSensorTask (실시간 데이터 생산자)

    - osDelayUntil()을 사용하여 10ms의 고정 주기로 정밀하게 동작한다.

    - 주기마다 깨어나 Update_Motor_RPM(), Ultrasonic_Trigger() 등을 호출하여 모든 센서 값을 최신 상태로 갱신한다.

    - 수집된 모든 데이터를 SensorData_t 구조체로 패키징하여 CANTxQueueHandle을 통해 CANTask에 전달한다.

```c
void StartSensorTask(void *argument)
{
  // ...
  uint32_t last_wake_time = osKernelGetTickCount();
  for(;;)
  {
    // 1. 10ms 주기를 정밀하게 유지
    last_wake_time += 10;
    osDelayUntil(last_wake_time);

    // 2. 모든 센서 데이터 수집 및 갱신
    Update_Motor_RPM();
    Ultrasonic_Trigger();

    // 3. 데이터 패킷 생성
    SensorData_t sensor_packet;
    sensor_packet.rpm = MotorControl_GetRPM();
    // ... (초음파, 조도 센서 값 패키징)

    // 4. 생성된 데이터를 CANTask로 전송
    osMessageQueuePut(CANTxQueueHandle, &sensor_packet, 0, 0);
  }
}
```

- StartCANTask (데이터 가공 및 전송 컨트롤러)

    - osMessageQueueGet()을 통해 CANTxQueueHandle에 새로운 데이터가 들어올 때까지 무한정 대기한다 (이벤트 기반 동작)

    - 데이터 수신 즉시, CAN 프로토콜에 맞게 데이터를 가공한다. (e.g., 거리->장애물 상태 비트마스크, RPM->2바이트 정수 분리)

    - 최종 가공된 데이터를 TxData 버퍼에 채우고 CAN_Send()를 호출하여 전송을 완료한다.

```c
void StartCANTask(void *argument)
{
    // ...
    SensorData_t received_packet;
    for(;;)
    {
        // 1. CANTxQueue에서 데이터 수신 대기
        if (osMessageQueueGet(CANTxQueueHandle, &received_packet, NULL, osWaitForever) == osOK)
        {
            // 2. 수신된 데이터를 CAN 형식에 맞게 가공
            uint8_t obstacle_status = 0;
            if (received_packet.distance_front <= 10) obstacle_status |= (1 << 0);
            if (received_packet.distance_rear <= 10) obstacle_status |= (1 << 1);
            TxData[0] = obstacle_status;

            uint16_t rpm_value = (uint16_t)received_packet.rpm;
            TxData[2] = (uint8_t)(rpm_value & 0x00FF);
            TxData[3] = (uint8_t)((rpm_value >> 8) & 0x00FF);

            // 3. 최종 데이터를 CAN 버스로 전송
            CAN_Send();
        }
    }
}

```

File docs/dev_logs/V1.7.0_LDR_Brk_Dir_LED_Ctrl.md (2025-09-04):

# LDR 기반 전/후진 및 브레이크 상태에 따라 전조등·후미등 제어 로직 추가 (v1.7.0)

## 동작 요약
주변 밝기(LDR)와 차량의 주행 상태(전진/후진, 브레이크)를 종합하여 차량의 조명을 자동으로 제어한다.
1. Sensor MCU는 조도 센서(LDR) 값을 읽어 주변이 어두워지면 '어두움' 상태를 CAN 통신으로 전송한다.
2. Central MCU는 무선 조종기(RF) 신호를 받아 '전진/후진' 및 '브레이크' 상태를 CAN 통신으로 전송한다.
3. Status MCU는 두 MCU로부터 받은 CAN 데이터를 종합하여 다음 조건에 따라 LED를 점등한다.
    - 전조등: 주변이 어둡고 전진 상태일 때만 ON
    - 후미등: 주변이 어둡고 후진 상태일 때만 ON
    - 브레이크등: 주변 밝기와 상관없이 브레이크가 작동될 때 항상 ON

---

## 하드웨어 연결

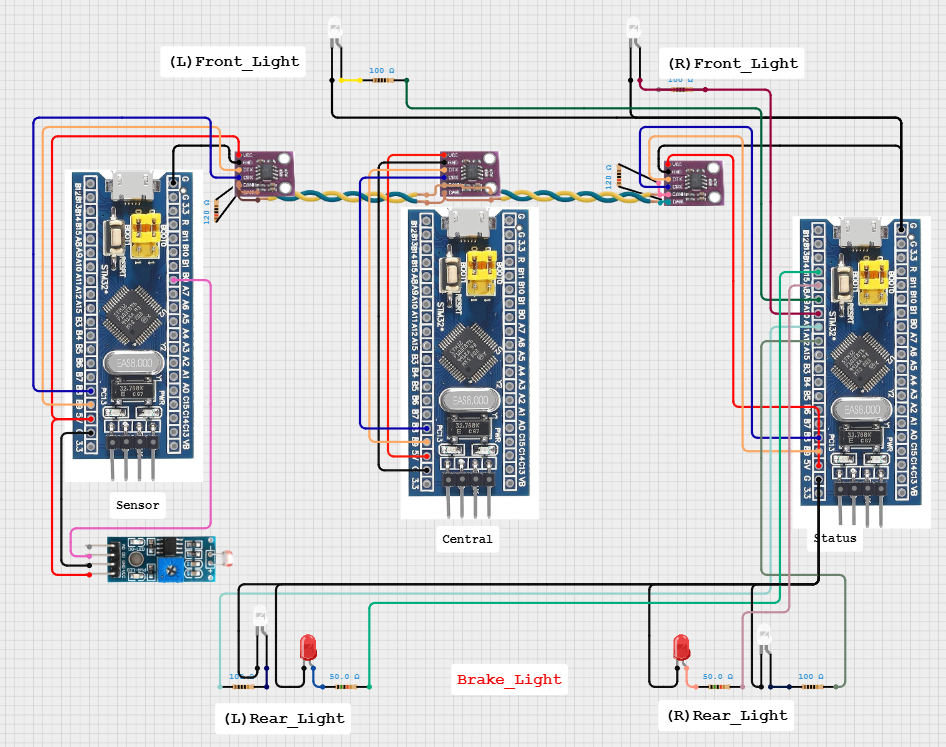
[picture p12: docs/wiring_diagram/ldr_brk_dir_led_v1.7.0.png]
ldr,brk,dir기반 LED 배선도


---

## STM32CubeMX 설정

### sensor부
- LDR_IN (GPIO_Input) : PB0

### status부
- REAR_RIGHT_LED (GPIO_Output) : PA12
- REAR_LEFT_LED (GPIO_Output) : PA11
- FRONT_RIGHT_LED (GPIO_Output) : PA10
- FRONT_LEFT_LED (GPIO_Output) : PA9
- BRAKE_RIGHT_LED (GPIO_Output) : PA8
- BRAKE_LEFT_LED (GPIO_Output) : PB15

---

## 코드 주요 로직

### 1. Sensor → Status: 조도(LDR) 데이터 전송
Sensor MCU는 조도 센서(LDR)를 읽어 주변이 어두운지 판단하고, 그 결과를 CAN ID 0x6A5 로 전송한다.

```c
// ... main 함수 내부 ...
uint8_t light_condition = HAL_GPIO_ReadPin(GPIOB, GPIO_PIN_0); 
if (light_condition == GPIO_PIN_RESET) 
  TxData[1] = 1; // 어두움 플래그
else
  TxData[1] = 0; // 밝음 플래그

CAN_Send();
```
- HAL_GPIO_ReadPin(GPIOB, GPIO_PIN_0): LDR 센서가 연결된 PB0 핀의 디지털 상태를 읽음 (어두울 때 Low(RESET) 신호가 들어오도록 설계)
- if (light_condition == GPIO_PIN_RESET): 만약 핀 상태가 Low라면, 어둡다고 판단
- TxData[1] = 1: 전송할 데이터의 두 번째 바이트([1])에 '어두움'을 의미하는 1을 저장합니다. 밝을 경우 0을 저장
- CAN_Send(): 이 TxData 배열을 포함한 CAN 메시지를 네트워크로 전송

### 2. Central → Status: 주행 및 브레이크 상태 전송
Central MCU는 RF 통신을 바탕으로 차량의 전진/후진 및 브레이크 상태를 CAN ID 0x321 로 전송한다.

```c
// ... main 함수 내부, RF 명령 수신 후 ...
// 전진/후진 + 브레이크 상태를 CAN으로 전송
uint8_t dir = cmd.direction;
uint8_t brake = (cmd.brake_ms > 0) ? 1 : 0; // 브레이크 명령이 있으면 1
CAN_Send_DriveStatus(dir, brake);

// <can_handler.c>
void CAN_Send_DriveStatus(uint8_t direction, uint8_t brake_status)
{
    CAN_TxHeaderTypeDef TxHeader;
    uint8_t TxData[2];
    uint32_t TxMailbox;

    TxHeader.StdId = 0x321;  // 메시지 ID: 0x321
    TxHeader.DLC = 2;        // 데이터 길이: 2바이트

    TxData[0] = direction;   // Data[0]: 방향 (1: 전진, 0: 후진)
    TxData[1] = brake_status;// Data[1]: 브레이크 (1: 작동, 0: 해제)

    HAL_CAN_AddTxMessage(&hcan, &TxHeader, TxData, &TxMailbox);
}
```
- main 함수에서 RF 명령(cmd)으로부터 방향(direction)과 브레이크 작동 여부(brake_ms > 0)를 추출
- CAN_Send_DriveStatus() 함수를 호출
- 이 함수는 ID 0x321 로 CAN 메시지를 설정하고, 전달받은 direction과 brake_status 값을 각각 데이터의 첫 번째와 두 번째 바이트에 담아 전송함

### 3. Status: CAN 데이터 수신 및 LED 점등
Status MCU는 Sensor와 Central로부터 CAN 메시지를 수신하여 상태를 종합하고, 최종 조건에 따라 전조등, 후미등, 브레이크등을 제어한다.

```c
// <can_handler.c>
// CAN 수신 인터럽트 콜백 함수
void HAL_CAN_RxFifo1MsgPendingCallback(CAN_HandleTypeDef *hcan)
{
    HAL_CAN_GetRxMessage(hcan, CAN_RX_FIFO1, &RxHeader, RxData);

    // Sensor로부터 온 조도 정보 처리 (ID: 0x6A5)
    if (RxHeader.StdId == 0x6A5 && RxHeader.DLC == 2)
    {
        // ... (status_distance = RxData[0];) ...
        status_light = RxData[1]; // 조도 상태 저장
    }
    // Central로부터 온 주행 정보 처리 (ID: 0x321)
    else if (RxHeader.StdId == 0x321 && RxHeader.DLC == 2)
    {
        status_direction = RxData[0]; // 주행 방향 저장
        status_brake = RxData[1];     // 브레이크 상태 저장
    }

    // 수신된 최신 정보로 LED 상태 즉시 업데이트
    LEDControl_Update(status_light, status_direction, status_brake);
}

// <led_control.c>
void LEDControl_Update(uint8_t ldr_dark, uint8_t direction, uint8_t brake)
{
    // ... (모든 LED 핀 초기화: OFF) ...

    // 전조등/후미등 제어 (어두울 때만)
    if (ldr_dark == 1) // status_light가 1이면(어두우면)
    {
        if (direction == 1) // 전진 시
        {
            // 전조등 2개 ON
            HAL_GPIO_WritePin(GPIOA, GPIO_PIN_9, GPIO_PIN_SET);
            HAL_GPIO_WritePin(GPIOA, GPIO_PIN_10, GPIO_PIN_SET);
        }
        else if (direction == 0) // 후진 시
        {
            // 후미등 2개 ON
            HAL_GPIO_WritePin(GPIOA, GPIO_PIN_11, GPIO_PIN_SET);
            HAL_GPIO_WritePin(GPIOA, GPIO_PIN_12, GPIO_PIN_SET);
        }
    }

    // 브레이크등 제어 (밝기와 무관)
    if (brake > 0) // 브레이크 상태가 1이면
    {
        // 브레이크등 2개 ON
        HAL_GPIO_WritePin(GPIOA, GPIO_PIN_8, GPIO_PIN_SET);
        HAL_GPIO_WritePin(GPIOB, GPIO_PIN_15, GPIO_PIN_SET);
    }
}
```
- HAL_CAN_RxFifo1MsgPendingCallback: CAN 메시지가 수신될 때마다 자동으로 실행되는 인터럽트 함수
- ID 0x6A5 수신 시: RxData[1](조도 정보) 값을 status_light 변수에 저장함
- ID 0x321 수신 시: RxData[0](방향), RxData[1](브레이크) 값을 각각 status_direction, status_brake 변수에 저장
- LEDControl_Update() 호출: 어떤 메시지를 받든, 콜백 마지막에서 이 함수를 호출해 즉시 LED 상태를 갱신함
- LEDControl_Update 함수 내부:
  - 전조등: 어둡고(ldr_dark == 1) 전진기어에 위치할 때 (direction == 1)라는 두 가지 조건이 모두 만족될 때만 켜짐
  - 후미등: 어둡고(ldr_dark == 1) 후진기어에 위치할 때 (direction == 0) 켜짐
  - 브레이크등: 브레이크가 작동 중(brake > 0) 이면, 주변 밝기나 주행 방향과 관계없이 항상 켜짐

---

## 문제 및 해결

### 문제 발생
LED 기능 추가 후 CAN 통신은 정상적으로 동작했으나, Central MCU와 컨트롤러 간의 RF 통신이 실패하는 문제가 발생

### 원인 분석 및 해결 과정

1. 모듈 테스트: m3_rf_comm 테스트 프로젝트를 통해 RF 모듈 개별 테스트를 진행한 결과, Central MCU에 연결된 트랜시버 모듈 자체의 고장으로 결론

2. 고장 원인 추정:
    - 브레드보드 내부의 잠재적인 단선 또는 접촉 불량
    -> 멀티미터로 실제 모듈 전압 측정 결과 3.2V로 정상 측정이 확인되어 쇼트 문제는 아닌 것으로 확인
    - 모듈 연결 시 실수로 3.3V가 아닌 5V 전원을 인가했을 가능성 (rf 트랜시버 모듈 datasheet 상 3.3v 연결 강조)
    - 코드의 비효율성으로 인한 모듈 과부하 및 회로 손상 가능성 

3. 해결:
    - 새 RF 트랜시버 모듈로 교체 후 모듈 테스트 결과 컨트롤러 측 모듈은 정상 동작 확인
    -> central부의 트랜시버 모듈이 고장인 것으로 확인
    - 회로의 물리적 안정성을 높이기 위해 Central MCU가 연결된 브레드보드를 새 것으로 교체
    - 추후 pcb설계를 통해 회로 안정화 필요 
 
---

## 향후 확장 및 개선 아이디어
- FreeRTOS 기반 CAN 통신 모듈화 및 태스크 분리
- PCB 제작을 통한 회로 안정화

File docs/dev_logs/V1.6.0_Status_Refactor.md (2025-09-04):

# Status 부 파일 분할 및 코드 최적화, CAN 개선, ADC 배터리측정 로직 추가 (v1.6.0)

## 파일 분할 및 코드 최적화 목적

기존 status_v1.5.0은 모든 기능이 main.c 하나에 집중되어 있어 코드의 복잡도가 높고 유지보수가 어려웠다. 특히, CAN 수신 처리, OLED 출력, 배터리 전압 측정 및 계산 등의 기능이 하나의 루프에서 혼합되어 처리되며, 기능 간의 명확한 역할 분리 부족, 디버깅의 어려움, 확장성 저하 등의 문제가 존재했다.

이를 해결하기 위해 status_v1.6.0에서는 다음과 같은 방식으로 기능별 모듈화 및 파일 분할을 수행하였다:

---

## 주요 변경 사항

### 1. 파일 분할 (모듈화)

기존 main.c의 역할을 분산시키고, 기능별 독립성을 확보하기 위해 아래와 같이 파일을 분할함

- `can_handler.c/.h` (CAN 수신 핸들러)
    - 역할: 거리 조건에 따른 CAN 수신 데이터를 처리하고, 수신된 RxData[0] 값을 해석하여 시스템 상태(Status: SAFE, DETECTED 등)를 판단함.
    - 주요 함수:
        - `CANHandler_Init()` : CAN 시작 및 필터/인터럽트 설정
        - `HAL_CAN_RxFifo1MsgPendingCallback()` : ID 0x6A5 수신 시 `RxData[0]` 값을 판별하여 OLED 상태 갱신 요청

- `battery_monitor.c/.h` (배터리 전압 모니터링)
    - 역할: ADC를 통해 배터리 전압을 측정하고, 이동 평균 필터와 보정 계수를 적용하여 안정적인 전압 값을 계산함. 해당 전압 값을 기준으로 퍼센트(%) 값을 산출하여 표시용으로 제공함.
    - 주요 함수:
        - `Read_Battery_Percentage()` : 보정 및 필터 적용된 전압 및 잔량(%) 반환
        - `Get_Averaged_Vout()` : 이동 평균 필터 적용

- `oled_display.c/.h` (OLED 출력 전담 모듈)
    - 역할: OLED 초기화 및 화면 갱신 처리. 배터리 상태 및 수신된 시스템 상태(Status: SAFE, DETECTED 등)를 화면에 출력함.
    - 주요 함수:
        - `OLED_Init()` : OLED 초기화 및 화면 클리어
        - `OLED_SetStatus()` : 상태 문자열 설정
        - `OLED_BatteryStatus()` : 배터리 퍼센트 및 전압을 화면에 출력

- `main.c`의 역할 변경
    - 역할: 시스템 초기화 이후 main 루프에서는 주기적으로 배터리 상태를 측정하고, 수신된 CAN 데이터에 따라 상태를 업데이트하는 등 전체 동작을 조율함. 각 기능은 각각의 전담 모듈로 위임되어, main.c는 중재자(Coordinator) 역할만 수행함.
    - 주요 처리 로직:
        - 100ms 주기로 배터리 전압 및 잔량 측정
        - `OLED_BatteryStatus()`를 통해 화면에 전압 및 상태 정보 표시
        - 수신된 CAN 메시지는 `can_handler.c`에서 직접 처리됨

### 2. 코드 구조 최적화

파일 분할을 통해 아래와 같은 코드 구조 개선을 진행하였다.

#### 데이터 흐름 명확화
- 내용: 
    - CAN으로 수신된 거리 위험 신호(RxData[0], 1: 위험 / 0: 안전)는 `can_handler.c` 내 인터럽트 콜백에서 직접 처리되며, `OLED_SetStatus()`를 호출하여 시스템 상태를 전역 문자열로 업데이트한다.
    - 배터리 전압은 `battery_monitor.c`에서 ADC를 통해 주기적으로 측정되며, 보정 및 이동 평균 필터를 거쳐 전압(V)과 잔량(%)으로 변환된다.
    - `main.c`는 일정 주기로 배터리 상태를 `OLED_BatteryStatus()`를 통해 출력한다.
- 효과 : 
    - CAN 수신 → 상태 문자열 업데이트 → OLED 표시, ADC 측정 → 전압/퍼센트 계산 → OLED 표시라는 단방향 흐름이 명확하게 분리되어 유지된다.
    - 전역 변수나 혼합된 처리 없이, 각 모듈의 데이터 입력과 출력 경로가 명확하여 디버깅, 추적, 기능 확장 등이 용이해짐

#### 캡슐화 및 책임 분리
- 내용 : 
    - `main.c`는 더 이상 하드웨어 세부 제어나 UI 업데이트를 직접 수행하지 않는다.
    - `can_handler.c`는 CAN 수신 및 수신 메시지 해석만을 담당하며, `OLED_SetStatus()`를 통해 상태 변경만 수행한다.
    - `battery_monitor.c`는 ADC 처리, 보정, 필터링, 퍼센트 계산을 전담한다.
    - `oled_display.c`는 OLED 초기화 및 출력 처리만을 담당하며, 외부로부터 받은 값만 출력하고 내부 로직을 드러내지 않음
- 효과 :
    - 각 기능별로 명확한 책임(Roles) 을 부여하여 모듈 간 결합도를 낮춤
    - 기능 추가나 수정 시 다른 모듈에 영향을 주지 않고 독립적으로 관리 가능
    - 각 모듈에 대해 단위 테스트 또는 독립 디버깅이 가능하여 유지보수성 향상 

### 3. 주요 개선 사항: 수신 반응 최적화 및 시스템 응답성 개선

status_v1.6.0에서는 CAN 수신 반응 처리 최적화와 OLED 출력 구조 정비, 배터리 모니터링 효율화를 통해 시스템 전반의 실시간 반응성과 안정성을 향상시켰다. 이를 통해 초음파 기반 거리 감지 결과를 수신한 후 OLED 출력까지의 End-to-End 반응 시간을 단축시켰으며, 실시간 상태 모니터링이 가능한 구조로 개선하였다.

#### 수신 응답 최적화
1. 인터럽트 기반 CAN 수신 구조 도입
    - 기존 Superloop 내 수신 대기 방식에서 벗어나, FIFO1 수신 인터럽트 콜백을 사용하여 거리 상태 메시지를 실시간으로 수신함.
    - 수신 후 즉시 `OLED_SetStatus()` 호출을 통해 지연 없이 사용자 피드백 가능.

2. OLED 출력 처리 구조 개선
    - 수신된 상태 문자열은 내부 전역 버퍼(`oled_line1`)에 저장되고, OLED는 별도 루프에서 주기적으로 배터리 상태와 함께 출력.
    - OLED 업데이트와 수신 처리를 분리하여 화면 깜빡임 최소화, 동시성 안정성 확보.

3. CAN 메시지 구조 경량화 수신 대응
    - 송신 노드에서는 `TxData[0]` 1바이트만 사용하며, status 노드는 해당 바이트만으로 상태 판별을 수행.
    - RxHeader.DLC 검증을 통해 불완전 패킷 방지, 수신 처리의 정확성과 안정성 강화.

#### 개선 효과
- 수신 반응 시간 단축
    - 거리 감지 후 CAN 수신 → 상태 출력까지의 전체 흐름이 인터럽트 기반으로 최적화되어, 사용자 피드백이 즉각적으로 이루어짐.

- 시스템 신뢰성 향상
    - 자동 재전송이 설정된 송신 노드 구조와 연동하여, status 노드에서는 누락 없는 신뢰성 있는 수신 처리가 가능해짐.

- 자원 효율성 개선
    - RxData의 유효 바이트만 활용하여 메모리 사용 최소화, OLED 출력도 최소한의 연산으로 수행하여 CPU 부하 절감.

- 확장성 확보
    - 추후 다양한 상태 메시지 유형 추가 또는 다중 센서 대응 시에도, 현재 구조에서 모듈 확장만으로 대응 가능하도록 설계됨.

---

## 주요 코드 설명

### `can_handler.h`: CAN 통신 모듈 인터페이스 정의
```c
#ifndef INC_CAN_HANDLER_H_
#define INC_CAN_HANDLER_H_

#include "main.h"

// =============================
// CAN 수신 메시지 설명:
// ID 0x6A5, RxData[0] = 거리 조건 (1: 위험, 0: 안전)
// =============================

extern CAN_FilterTypeDef sFilterConfig;
extern CAN_RxHeaderTypeDef RxHeader;
extern uint8_t RxData[8];

void CANHandler_Init(void);               // CAN 시작 + 필터 + 인터럽트 설정
void CAN_Filter_Config(CAN_HandleTypeDef *hcan_ptr);  // 필터 구성
void HAL_CAN_RxFifo1MsgPendingCallback(CAN_HandleTypeDef *hcan);  // 수신 콜백

#endif /* INC_CAN_HANDLER_H_ */
```
- `CANHandler_Init()`
    - CAN 시작, 필터 설정, 인터럽트 활성화 수행

- `CAN_Filter_Config()`
    - ID 0x6A5만 수신할 수 있도록 마스크 필터 설정 (표준 ID, DLC 1 기준)

- `HAL_CAN_RxFifo1MsgPendingCallback()`
    - 수신 메시지를 읽고 RxData[0] 값에 따라 OLED 상태를 설정 (SAFE, DETECTED, UNKNOWN)

### `can_handler.c`: CAN 통신 모듈 구현
```c
#include "can_handler.h"
#include "can.h"
#include "oled_display.h"

CAN_FilterTypeDef sFilterConfig;
CAN_RxHeaderTypeDef RxHeader;
uint8_t RxData[8];

extern char oled_line1[21];

void CANHandler_Init(void)
{
    extern CAN_HandleTypeDef hcan;
    HAL_CAN_Start(&hcan);
    CAN_Filter_Config(&hcan);
}

void CAN_Filter_Config(CAN_HandleTypeDef *hcan_ptr)
{
    sFilterConfig.FilterActivation = CAN_FILTER_ENABLE;
    sFilterConfig.FilterFIFOAssignment = CAN_FILTER_FIFO1;
    sFilterConfig.FilterMode = CAN_FILTERMODE_IDMASK;
    sFilterConfig.FilterIdHigh = 0x6A5 << 5;
    sFilterConfig.FilterIdLow = 0;
    sFilterConfig.FilterMaskIdHigh = 0x7FF << 5;
    sFilterConfig.FilterMaskIdLow = 0;
    sFilterConfig.FilterScale = CAN_FILTERSCALE_32BIT;

    if (HAL_CAN_ConfigFilter(&hcan, &sFilterConfig) != HAL_OK)
        Error_Handler();

    if (HAL_CAN_ActivateNotification(&hcan, CAN_IT_RX_FIFO1_MSG_PENDING) != HAL_OK)
        Error_Handler();
}

void HAL_CAN_RxFifo1MsgPendingCallback(CAN_HandleTypeDef *hcan)
{
    HAL_CAN_GetRxMessage(hcan, CAN_RX_FIFO1, &RxHeader, RxData);

    if (RxHeader.StdId == 0x6A5 && RxHeader.DLC == 1)
    {
        if (RxData[0] == 1)
            OLED_SetStatus("DETECTED");
        else if (RxData[0] == 0)
            OLED_SetStatus("SAFE");
        else
            OLED_SetStatus("UNKNOWN");
    }
}
```
- 전역 변수 선언
    - `CAN_FilterTypeDef sFilterConfig`
    → CAN 수신 필터 설정 구조체 (ID/마스크 구성용)
    - `CAN_RxHeaderTypeDef RxHeader`
    → 수신된 CAN 메시지의 헤더 정보 저장 (ID, DLC 등)
    - `uint8_t RxData[8]`
    → 수신된 데이터 저장용 배열. 현재는 RxData[0]만 유효 (거리 상태: 1 or 0)

- `CANHandler_Init()`
    - 역할: 전체 CAN 수신 기능 초기화
    - 동작:
        - `HAL_CAN_Start()`로 CAN 주변장치 동작 시작
        - `CAN_Filter_Config()` 호출 → 수신 필터 및 인터럽트 설정

- `CAN_Filter_Config()`
    - 역할: 수신 필터 및 인터럽트 활성화 설정
    - 주요 설정 내용:
        - 필터 모드: ID 마스크 방식
        - 허용 ID: 0x6A5 (<<5 시프트는 11비트 ID를 필터 레지스터에 맞춤)
        - 마스크: 0x7FF (전체 11비트 일치 요구)
        - 필터 대상 FIFO: FIFO1
        - 인터럽트 활성화: `CAN_IT_RX_FIFO1_MSG_PENDING`

    → 이 설정으로, ID 0x6A5의 CAN 메시지가 도착하면 FIFO1 인터럽트로 수신된다.

- `HAL_CAN_RxFifo1MsgPendingCallback()`
    - 역할: 수신 메시지가 도착했을 때 자동 호출되는 인터럽트 콜백
    - 동작 흐름:
        1. HAL_CAN_GetRxMessage()로 수신 메시지를 RxHeader, RxData에 저장
        2. StdId가 0x6A5이고, 데이터 길이 DLC == 1이면 유효한 메시지로 간주
        3. RxData[0]의 값에 따라 OLED에 상태 문자열 설정
            - 1 → "DETECTED"
            - 0 → "SAFE"
            - 기타 → "UNKNOWN"

    → 이후 실제 OLED 화면 출력은 main.c 루프에서 OLED_BatteryStatus()를 통해 주기적으로 갱신됨

### `battery_monitor.h`: 배터리 측정 모듈 인터페이스 정의
```c
#ifndef INC_BATTERY_MONITOR_H_
#define INC_BATTERY_MONITOR_H_

#include "main.h"

float Read_Battery_Percentage(float* vout_ret);
float Get_Averaged_Vout(float new_sample);

#endif /* INC_BATTERY_MONITOR_H_ */
```

- `Read_Battery_Percentage()`
    - ADC로 측정한 값을 기반으로 배터리 전압을 계산하고, 보정 및 이동 평균 필터를 적용한 후 최종 퍼센트(%)로 환산하여 반환
    - `vout_ret` 포인터가 전달되면, 보정 및 필터가 적용된 Vout 값(전압)을 함께 반환

- `Get_Averaged_Vout()`
    - 최근 N개의 전압 샘플에 대한 이동 평균을 계산하여 노이즈를 줄이고 측정값의 안정성을 확보
    - 내부적으로 순환 버퍼를 사용하여 필터링 처리

이 헤더는 배터리 상태를 수치화하고 OLED 출력에 활용하기 위한 전압/잔량 계산 인터페이스를 제공함.
main.c에서는 이 모듈을 호출하여 주기적으로 배터리 상태를 모니터링할 수 있음.

### `battery_monitor.c`: 배터리 측정 모듈 구현
```c
#include "battery_monitor.h"
#include "adc.h"

// 이동 평균 필터 내부 변수
#define FILTER_SIZE 10
#define VOUT_CORRECTION_FACTOR 1.010f

// 내부 변수
float vout_buffer[FILTER_SIZE] = {0};  // 최근 10개 저장
uint8_t filter_index = 0;
uint8_t valid_sample_count = 0;

// 이동 평균 계산 함수
float Get_Averaged_Vout(float new_sample)
{
    vout_buffer[filter_index] = new_sample;
    filter_index = (filter_index + 1) % FILTER_SIZE;

    if (valid_sample_count < FILTER_SIZE)
        valid_sample_count++;

    float sum = 0.0f;
    for (int i = 0; i < valid_sample_count; i++)
        sum += vout_buffer[i];

    return sum / valid_sample_count;
}

//--- adc 전압출력 및 배터리 전압 → 퍼센트 계산 함수 ---
float Read_Battery_Percentage(float* vout_ret)
{
    HAL_ADC_Start(&hadc1);
    HAL_ADC_PollForConversion(&hadc1, HAL_MAX_DELAY);
    uint16_t adc_val = HAL_ADC_GetValue(&hadc1);
    HAL_ADC_Stop(&hadc1);

    // 1. ADC → STM32 입력 전압 (Vout raw)
    float vout_raw = (3.3f * adc_val) / 4095.0f;

    // 2. 고정 보정 계수 적용
    float vout = vout_raw * VOUT_CORRECTION_FACTOR;

    // 3. 이동 평균 필터 적용
    vout = Get_Averaged_Vout(vout);

    // 4. 분압 비율에 따라 Vbat 복원 (ex: 11.46V → 2.92V 였다면)
    float vbat = vout * (11.46f / 2.92f);  // 실측 기반 비율

    // 5. Vbat → 퍼센트 환산 (최대 12.6V, 최소 9.6V 기준)
    float percent = ((vbat - 9.6f) / (12.6f - 9.6f)) * 100.0f;

    // 6. 범위 제한
    if (percent > 100.0f) percent = 100.0f;
    if (percent < 0.0f) percent = 0.0f;

    if (vout_ret != NULL)
        *vout_ret = vout;

    return percent;
}
```
- 전역 변수
    - vout_buffer[]: 최근 N개의 전압 샘플을 저장하는 이동 평균 필터용 버퍼
    - filter_index: 버퍼에서 새 샘플을 저장할 위치를 가리키는 인덱스
    - valid_sample_count: 필터 적용을 위한 유효 샘플 개수
    - VOUT_CORRECTION_FACTOR: ADC 오차 보정을 위한 계수 (실측 기반으로 조정)

- `Get_Averaged_Vout()` 함수
    - 새로운 전압 샘플을 버퍼에 저장하고, 최근 유효한 샘플들의 평균을 계산
    - 순환 버퍼(Circular Buffer) 구조를 사용해 메모리 효율을 높이고, 이동 평균을 통해 노이즈를 줄여 전압 측정의 안정성 확보

- `Read_Battery_Percentage()` 함수
    - 역할: ADC로 측정한 전압 값을 기반으로, 보정 및 필터링을 거쳐 배터리 잔량(%)과 전압(Vout) 을 계산
    - 동작 순서:
        1. ADC 값 읽기 → STM32 입력 전압(Vout) 계산
        2. 보정 계수 적용 (VOUT_CORRECTION_FACTOR)
        3. 이동 평균 필터로 노이즈 제거
        4. 실측 분압 비율을 통해 실제 배터리 전압(Vbat) 복원
    - 출력:
        - 반환값: 배터리 잔량(%)
        - vout_ret 포인터가 전달되면 필터링된 전압 값도 함께 반환

### `oled_display.h`: OLED 출력 관련 모듈 인터페이스
```c
#ifndef INC_OLED_DISPLAY_H_
#define INC_OLED_DISPLAY_H_

#include <stdint.h>

void OLED_Init(void);  // 외부에서 호출할 초기화 함수
// OLED 상태 정보 표시 함수
void OLED_BatteryStatus(const char* status, float percent, float vout);
void OLED_SetStatus(const char* status);

#endif /* INC_OLED_DISPLAY_H_ */
```

- OLED 화면에 시스템 상태(Status), 배터리 전압(V), 잔량(%)을 출력하기 위한 표시 전용 인터페이스 정의

- `OLED_Init(void)`
    - SSD1306 OLED 초기화 및 화면 클리어 수행
    - 시스템 시작 시 한 번 호출되어야 함

- `OLED_SetStatus(const char* status)`
    - 상태 문자열(예: "SAFE", "DETECTED", "UNKNOWN")을 내부 버퍼에 저장
    - 실제 출력은 별도 함수(OLED_BatteryStatus)에서 처리됨

- `OLED_BatteryStatus(const char* status, float percent, float vout)`
    - 상태 문자열, 배터리 퍼센트, 전압 정보를 OLED에 출력
    - status가 NULL일 경우 이전에 저장된 상태 문자열 사용
    - 호출 시 화면 전체를 갱신함

### `oled_display.c`: OLED 출력 관련 모듈 구현
```c
#include "oled_display.h"
#include "ssd1306.h"
#include "fonts.h"
#include <stdio.h>
#include <string.h>

static char oled_line1[21] = "Status: ---";
static char oled_line2[21];
static char oled_line3[21];

void OLED_Init(void)
{
    SSD1306_Init();
    SSD1306_Clear();
    SSD1306_UpdateScreen();
}

void OLED_SetStatus(const char* status)
{
    snprintf(oled_line1, sizeof(oled_line1), "Status: %s", status);
}

void OLED_BatteryStatus(const char* status, float percent, float vout)
{
    if (status != NULL)
        OLED_SetStatus(status); // 상태 문자열 갱신

    // 배터리 계산 후 문자열 구성
    snprintf(oled_line2, sizeof(oled_line2), "BAT: %3d%%", (uint8_t)(percent + 0.5f)); // 소수점 반올림
	snprintf(oled_line3, sizeof(oled_line3), "VOL: %.2fV", vout);

	SSD1306_Clear();
	SSD1306_GotoXY(0, 0);  SSD1306_Puts(oled_line1, &Font_7x10, 1);
	SSD1306_GotoXY(0, 20); SSD1306_Puts(oled_line2, &Font_7x10, 1);
	SSD1306_GotoXY(0, 30); SSD1306_Puts(oled_line3, &Font_7x10, 1);
	SSD1306_UpdateScreen();
}
```

- OLED 화면에 시스템 상태(Status), 배터리 잔량(%), 전압(V)을 구조적으로 출력하는 전담 모듈

- 전역 버퍼
    - oled_line1[21]
    → 상태 문자열 저장 (예: "Status: SAFE")
    - oled_line2[21]
    → 배터리 잔량 표시 문자열 (예: "BAT: 87%")
    - oled_line3[21]
    → 배터리 전압 표시 문자열 (예: "VOL: 3.04V")

    버퍼를 전역으로 유지하여 화면 갱신 시 일관된 문자열 구성을 보장함

- `OLED_Init()`
    - SSD1306 OLED 디스플레이 초기화
    - 화면 클리어 후 초기 상태 출력 준비

- `OLED_SetStatus(const char* status)`
    - 전달받은 상태 문자열을 oled_line1에 포맷팅하여 저장
    - 화면 즉시 갱신은 하지 않음 → 분리된 출력 함수에서 사용

- `OLED_BatteryStatus(const char* status, float percent, float vout)`
    - 선택적으로 상태 문자열을 갱신 (status != NULL일 경우)
    - 배터리 잔량과 전압을 텍스트로 포맷하여 oled_line2, oled_line3에 저장
    - 이후 OLED 화면을 클리어하고 모든 줄을 다시 출력
    - SSD1306_UpdateScreen() 호출로 실제 화면에 적용

### `main.c` 의 개선

기존(v1.5.0)의 main.c는 CAN 수신 처리, OLED 상태 표시, 배터리 전압 측정 및 계산 등 모든 기능이 한 파일 내에 직접 구현되어 있었으며, 기능 간 경계가 불명확하고 복잡하고 비직관적인 구조였다.

모든 로직이 while(1) 루프 내에서 처리되다 보니 유지보수가 어렵고, 각 기능의 수정 시 전체 코드에 영향을 미치는 밀접 결합 구조를 갖고 있었다.

v1.6.0에서는 기능별 모듈을 명확히 분리하여 main.c는 시스템 흐름만 제어하는 중재자 역할만 담당하도록 개선되었다:

```c
while (1)
{
    if (HAL_GetTick() - last_update_time >= 100)
    {
        last_update_time = HAL_GetTick();

        float vout = 0.0f;
        float percent = Read_Battery_Percentage(&vout);

        OLED_BatteryStatus(NULL, percent, vout);
    }
}
```
- CAN 수신 및 상태 해석은 `can_handler.c`에서 인터럽트 기반으로 처리
- 배터리 전압 측정 및 필터링은 `battery_monitor.c`에서 전담
- OLED 출력 구성 및 갱신은 `oled_display.c`에서 관리
- `main.c`는 단지 주기 체크 + 배터리 측정 + OLED 호출만 수행

이로 인해 얻는 이점은 다음과 같다:

- 가독성 향상 : main.c는 시스템의 흐름만 담당하며, 각 기능은 명확히 분리되어 있어 코드 구조가 직관적이고 이해하기 쉬움

- 유지보수 용이 : 오류 발생 시 해당 모듈만 점검하면 되므로, 디버깅 범위가 좁아지고 안정성이 향상됨

- 확장성 증가 : 새로운 센서, 표시 항목 추가, 경고 시스템 등 추가 시 기존 코드 수정 없이 모듈 추가만으로 확장 가능

- 재사용성 강화 : battery_monitor.c, oled_display.c, can_handler.c 등은 다른 프로젝트나 보드에서도 독립적으로 재사용 가능

- 실시간성 확보 기반 마련 : 로직이 모듈화되어 있으므로, 향후 FreeRTOS 등 RTOS 환경으로 이식 시 Task 단위로 쉽게 분리 가능

---

## 향후 확장 방향: RTOS 도입을 통한 시스템 고도화

status_v1.6.0에서는 CAN 수신 처리의 인터럽트 기반 분리, 배터리 모니터링 모듈화, OLED 출력 구조 정비, main.c 단순화를 통해 기존의 while(1) 중심 Superloop 구조를 RTOS 기반의 태스크 중심 처리 방식으로 전환할 수 있는 토대를 마련하였다.
앞으로 시스템의 실시간 반응성, 안정성, 확장성을 더욱 향상시키기 위해 FreeRTOS 도입을 통해 현재의 순차적 처리 구조를 멀티태스킹(Multi-tasking) 구조로 전환할 계획이다.

### RTOS 도입의 필요성 및 기대 효과

현재 구조는 CAN 수신 처리 → 상태 갱신 → 배터리 측정 → OLED 출력 순서로 동작한다. 이 구조는 간단하지만, CAN 메시지 수신 빈도가 높아지거나 향후 다른 기능이 추가될 경우 다음과 같은 문제가 발생할 수 있다.

- 처리 지연: OLED 업데이트와 같이 상대적으로 느린 작업이 수행되는 동안 중요한 CAN 메시지 처리가 지연될 수 있다.
- 기능 간섭: 모든 기능이 하나의 실행 흐름(Context)에서 동작하므로, 한 기능의 변경이 다른 기능에 예기치 않은 영향을 줄 수 있다.

RTOS를 적용하면 각 기능을 독립적인 **태스크(Task)**로 분리하여 이러한 문제를 해결하고 다음과 같은 효과를 기대할 수 있다.

- 실시간 응답성 확보: CAN 데이터 처리처럼 시간 제약이 중요한 작업에 높은 우선순위를 부여하여, 디스플레이 업데이트와 같은 다른 작업에 의해 실행이 방해받지 않도록 보장한다.
- 시스템 확장성 향상: 향후 자가 진단, 로그 전송 등 새로운 기능을 기존 코드에 영향을 주지 않고 독립된 태스크 단위로 안전하게 추가할 수 있다.
- 안정성 및 신뢰성 증대: 메시지 큐(Message Queue)를 통해 태스크 간 데이터 전송을 안전하게 관리하여 데이터 손실이나 오염을 방지하고, 시스템의 전체적인 안정성을 높일 수 있다.

### 단계별 RTOS 적용 계획

#### 1단계: 기능 분리 및 태스크화
가장 먼저, 현재 순차적으로 실행되는 주요 기능들을 역할에 따라 두 개의 독립적인 태스크로 분리할 것이다.

- CANTask: CAN 버스로부터 들어오는 모든 메시지를 수신하여 처리하고, 통신 상태를 진단하는 데이터 처리 전담 태스크로 설계한다.
- DisplayTask: CANTask가 처리한 최종 데이터를 기반으로 LED 및 OLED 디스플레이 출력을 총괄하는 사용자 인터페이스 전담 태스크로 설계한다. 배터리 측정 로직은 이 태스크 내에서 주기적으로 수행하도록 통합한다.

#### 2단계: 태스크 간 통신 구조 설계
분리된 태스크들이 데이터를 안전하고 효율적으로 주고받을 수 있도록 메시지 큐 기반의 통신 구조를 설계할 것이다.

- 인터럽트 → 태스크 통신: CAN 수신 인터럽트(ISR)는 수신 데이터를 직접 처리하지 않고, CANRxQueue라는 메시지 큐에 삽입한다. CANTask는 이 큐에 데이터가 들어올 때까지 대기하다가, 데이터 수신 시 즉시 처리하여 ISR의 작업 부하를 최소화한다.
- 태스크 → 태스크 통신: CANTask는 수집된 모든 데이터를 가공하고 통신 상태를 진단한 뒤, DisplayDataQueue라는 별도의 큐를 통해 DisplayTask로 최종 상태 정보를 전달한다. 이를 통해 데이터 처리 로직과 출력 로직을 완벽히 **분리(Decoupling)**한다.

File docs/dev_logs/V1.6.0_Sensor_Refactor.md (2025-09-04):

# Sensor 부 파일 분할 및 코드 최적화, CAN 개선 (v1.6.0)

## 파일 분할 및 코드 최적화 목적

기존 sensor_v1.5.0은 모든 기능이 main.c 하나에 집중되어 있어 코드 복잡도가 높고 유지보수가 어려웠다. 특히, 초음파 센서 제어 로직과 CAN 메시지 송신 처리가 하나의 루프에서 직접 처리되며, 코드의 가독성 저하, 기능별 독립성 부족, 디버깅 어려움 등의 문제가 존재했다.
이를 해결하기 위해 sensor_v1.6.0에서는 다음과 같은 방식으로 기능별 모듈화 및 파일 분할을 수행하였다.

---

## 주요 변경 사항

### 1. 파일 분할 (모듈화)

기존 `main.c`의 역할을 분산시키고, 기능별 독립성을 확보하기 위해 아래와 같이 파일을 분할함

- `can_handler.c/.h` (CAN 통신 핸들러)
    - 역할: CAN 초기화 및 거리 조건에 따른 송신 데이터를 설정하고, 이를 CAN 메시지로 전송함. 송신 메시지는 다른 노드에서 위험 감지를 판단할 수 있도록 TxData[0]에 1 또는 0을 설정해 전송.

    - 주요 함수 : `CAN_tx_Init()` : CAN 시작 및 송신 헤더 설정, `CAN_Send()` : 설정된 데이터를 CAN 메시지로 전송

- `ultrasonic.c/.h` (초음파 센서 핸들러)
    - 역할 : 전방(PA9 트리거, PB6 에코) 및 후방(PA8 트리거, PB5 에코) 초음파 센서의 거리 측정을 담당함. 타이머 입력 캡처 인터럽트를 통해 Echo 신호를 측정하고, 거리값을 계산하여 전역 변수로 저장함.
    
    주요 함수 : `Ultrasonic_Init()` : 타이머 및 인터럽트 초기화, `Ultrasonic_Trigger()` : 두 초음파 센서에 트리거 신호 발생, `HAL_TIM_IC_CaptureCallback()` : 입력 캡처 인터럽트 기반 거리 측정 수행

- `main.c`의 역할 변경
    - 역할 : 시스템 초기화 이후 main() 루프에서 주기적으로 초음파 트리거를 발생시키고, 측정된 전방/후방 거리 값을 기반으로 위험 감지 여부를 판단하여 CAN 메시지를 송신함. 직접적인 거리 측정 로직이나 CAN 송신 코드는 모두 ultrasonic.c 및 can_handler.c에 위임되며, main.c는 전반적인 흐름을 조율하는 중재자(Coordinator) 역할을 수행함.

    - 주요 처리 로직:
        - 100ms 주기로 거리 측정 트리거
        - 전방 또는 후방 거리 중 하나라도 10cm 이하일 경우 위험 상태 전송 (TxData[0] = 1), 그렇지 않으면 안전 상태 전송 (TxData[0] = 0)

### 2. 코드 구조 최적화

파일 분할을 통해 아래와 같은 코드 구조 개선을 진행하였다.

#### 데이터 흐름 명확화
- 내용: 
    - 초음파 센서에서 측정된 거리 값은 ultrasonic.c 내부에서 distance_front, distance_rear 전역 변수에 저장된다.
    - main.c에서는 해당 거리 값을 기준으로 위험 여부를 판단하고, 이를 TxData[0]에 반영한 후 CAN_Send() 함수를 통해 메시지를 송신한다.
    - TxData[0]의 값(1: 위험, 0: 안전)은 수신 노드에서 햅틱 피드백 또는 OLED 출력 등에 활용된다.

- 효과 : 
    - 거리 측정 → 거리 판단 → CAN 전송이라는 단방향 흐름이 명확히 유지되며, 각 단계에서의 데이터 사용 위치가 명확하다.
    - 전역 변수의 혼용을 최소화하고, 각 모듈이 정의된 데이터 흐름만 처리하게 하여 디버깅과 추적이 용이해짐

#### 캡슐화 및 책임 분리
- 내용 : 
    - main.c는 더 이상 거리 측정 세부 처리(IC 캡처, 타이머 설정)나 CAN 전송 데이터 구성 세부 사항을 직접 다루지 않는다.
    - ultrasonic.c는 거리 측정만, can_handler.c는 송신 메시지 처리만 담당한다.
    - main.c는 타 주기적 로직의 흐름 제어만 담당하며, 하드웨어 세부 동작은 각 모듈에 위임됨
        - 예: Ultrasonic_Trigger()는 트리거 신호만 발생시킴 (내부 딜레이 포함)
        - CAN_Send()는 설정된 TxData[]를 이용해 송신만 수행하며, 메시지 구성은 main.c에서 판단하여 설정

- 효과 :
    - 각 모듈이 명확한 책임을 가지므로 모듈 간 결합도가 낮아지고,
    - 기능 추가/수정 시 다른 파일에 영향을 거의 주지 않음
    - 단위 테스트 또는 모듈 단독 테스트 수행이 쉬워져 유지보수성 및 확장성이 향상됨 

### 3. 주요 개선 사항: 통신 성능 최적화

sensor_v1.6.0에서는 초음파 거리 감지 결과를 보다 빠르고 안정적으로 전송하기 위해 CAN 통신 성능 최적화를 중점적으로 수행하였다. 이를 통해 거리 정보의 실시간 전송이 가능해졌으며, 햅틱 반응 등 응답성이 요구되는 기능에서도 End-to-End 지연 시간을 최소화하였다.

#### CAN 통신 최적화
1. 보드레이트 향상
    - CAN의 Prescaler 값을 72 → 18로 조정하여, 125kbps → 500kbps의 고속 통신 환경으로 개선함.
    - 초음파 센서 측정 후 거리 정보 전송 딜레이가 크게 감소, 햅틱 등 수신 노드의 반응 시간이 단축됨.

2. 자동 재전송 및 오류 복구 기능 활성화
    - AutoBusOff, AutoRetransmission 기능을 활성화하여 일시적 충돌이나 에러 상황에서도 자동으로 복구 및 재송신이 수행되도록 설정.
    - 안정적인 CAN 통신 유지로, 거리 정보가 누락되지 않으며 실시간성을 보장함.

3. 송신 데이터 패킷 구조 단순화 및 데이터 길이 최적화
    - 거리 정보는 위험(1) / 안전(0)의 1비트 신호만 전달되므로, TxData[0] 하나의 바이트만 사용
    - TxHeader.DLC 값을 8 → 1로 변경하여 실제 전송 데이터 길이와 일치시킴
    - TxData[] 배열 크기를 8 → 1로 축소하여 메모리 할당 범위 정비

#### 개선 효과

- End-to-End 지연 시간 최소화 : 초음파 트리거 → 거리 측정 → CAN 전송 → 수신 노드 반응까지의 전체 흐름이 최적화되어, 거리 변화에 대한 시스템 반응이 즉각적으로 동작함

- 시스템 안정성 향상 : 일시적인 에러나 노이즈 상황에서도 자동 복구 기능으로 연속적인 거리 상태 전송이 보장되며, 수신 누락 가능성이 현저히 감소

- 확장성 기반 마련 : 고속 CAN 설정을 통해 이후 다중 거리 센서, 다양한 경고 장치, 여러 수신 노드가 존재하는 구조로의 확장도 무리 없이 대응 가능

- 송신 데이터 패킷 구조 최적화 : 불필요한 데이터를 제거하고 전송 길이를 최소화함으로써 패킷 전송 속도가 향상되고, CAN 버스의 대역폭 점유율이 감소하여 전체 통신 효율이 높아짐. 또한 수신 노드의 반응 속도가 빨라지고, TxData 배열 크기 축소를 통해 메모리 사용량도 줄어드는 등 시스템 자원의 효율성이 전반적으로 개선

---

## 주요 코드 설명

### `can_handler.h`: CAN 통신 모듈 인터페이스 정의
```c
#ifndef INC_CAN_TX_HANDLER_H_
#define INC_CAN_TX_HANDLER_H_

#include "main.h"

extern CAN_TxHeaderTypeDef TxHeader;
extern uint32_t TxMailbox;
extern uint8_t TxData[1];

void CAN_tx_Init(void);   /* HAL_CAN_Start + 헤더 설정 */
void CAN_Send(void);   /* TxData[0] 전송 */

#endif /* INC_CAN_TX_HANDLER_H_ */
```
- CAN_tx_Init()
    - CAN 통신을 시작하고, 송신용 TxHeader를 설정 (표준 ID, Data Frame, DLC = 8)
    - 메시지 전송을 위한 기본 설정 함수

- CAN_Send()
    - TxData[] 배열에 설정된 데이터를 CAN 메시지로 전송
    - 센서부에서는 TxData[0]에 위험 여부(1 또는 0)를 설정하여 전송함

- extern 변수
    - TxHeader, TxMailbox, TxData[]를 다른 모듈(main.c 등)에서 접근할 수 있도록 외부 선언 처리

### `can_handler.c`: CAN 통신 모듈 구현
```c
#include "can_handler.h"
#include "can.h"

CAN_TxHeaderTypeDef TxHeader;
uint32_t TxMailbox;
uint8_t TxData[1]; // 외부 접근을 위해 전역 선언

void CAN_tx_Init(void)
{
	HAL_CAN_Start(&hcan);

	TxHeader.DLC = 1;  // data length : 1바이트만 전송
	TxHeader.IDE = CAN_ID_STD;
	TxHeader.RTR = CAN_RTR_DATA;
	TxHeader.StdId = 0x6A5;  // ID can be between Hex1 and Hex7FF (1-2047 decimal)
}

void CAN_Send(void)
{
	HAL_CAN_AddTxMessage(&hcan, &TxHeader, TxData, &TxMailbox);
}
```

- 전역 변수 선언
    - `TxHeader`: 송신 메시지의 헤더 정보(ID, 데이터 길이, Frame 유형 등)
    - `TxMailbox`: 메시지 전송을 위한 Mailbox 식별자
    - `TxData[1]`: 전송할 데이터 배열, 현재는 1바이트(위험 여부만 전달)

- `CAN_tx_Init()` 함수
    - CAN 통신을 시작하고(HAL_CAN_Start), 전송 메시지의 기본 헤더를 설정
    - 송신 ID는 0x6A5로 고정, 데이터 프레임이며 길이는 1바이트로 구성

- `CAN_Send()` 함수
    - `TxData[0]`에 담긴 데이터를 CAN 메시지로 전송
    - 전송 시 설정된 TxHeader 정보와 함께 CAN Mailbox에 추가됨
    - 센서 노드에서는 초음파 센서 판별 결과(1: 위험, 0: 안전)를 이 배열에 기록 후 호출

### `ultrasonic.h`: 초음파센서 모듈 인터페이스 정의
```c
#ifndef INC_ULTRASONIC_H_
#define INC_ULTRASONIC_H_

#include "main.h"

// 다른 파일(main.c 등)에서 사용할 수 있게 extern 선언
extern volatile uint32_t distance_front;
extern volatile uint32_t distance_rear;

void delay_us(uint16_t us);
void Ultrasonic_Init(void);
void Ultrasonic_Trigger(void);

#endif /* INC_ULTRASONIC_H_ */
```

- 거리값 변수는 extern volatile로 선언되어 다른 모듈에서 공유 가능
- delay_us()는 정확한 트리거 펄스 생성 및 시간 측정을 위한 핵심 유틸리티 함수
- Ultrasonic_Init(), Ultrasonic_Trigger()는 센서 사용을 위한 초기화 및 트리거 인터페이스 제공

### `rf_handler.c`: RF 통신 모듈 구현
```c
#include "ultrasonic.h"
#include "tim.h"

/* 외부 핸들 */
extern TIM_HandleTypeDef htim2;
extern TIM_HandleTypeDef htim4;

// 전역변수
volatile uint32_t ic_val1_front = 0;
volatile uint32_t ic_val2_front = 0;
volatile uint8_t is_first_captured_front = 0;
volatile uint32_t distance_front = 0;

volatile uint32_t ic_val1_rear = 0;
volatile uint32_t ic_val2_rear = 0;
volatile uint8_t is_first_captured_rear = 0;
volatile uint32_t distance_rear = 0;

// tim2를 delay로 사용
void delay_us(uint16_t us)
{
  __HAL_TIM_SET_COUNTER(&htim2, 0);
  while (__HAL_TIM_GET_COUNTER(&htim2) < us);
}

// 모듈 초기화
void Ultrasonic_Init(void)
{
	HAL_TIM_Base_Start(&htim2);  // 타이머 카운터만 시작
	HAL_TIM_IC_Start_IT(&htim4, TIM_CHANNEL_1);
	HAL_TIM_IC_Start_IT(&htim4, TIM_CHANNEL_2);
}

void Ultrasonic_Trigger(void)
{
	// 1) 전방 트리거
	HAL_GPIO_WritePin(GPIOA, GPIO_PIN_9, GPIO_PIN_SET);
	delay_us(10);
	HAL_GPIO_WritePin(GPIOA, GPIO_PIN_9, GPIO_PIN_RESET);

	// 2) 후방 트리거
	HAL_GPIO_WritePin(GPIOA, GPIO_PIN_8, GPIO_PIN_SET);
	delay_us(10);
	HAL_GPIO_WritePin(GPIOA, GPIO_PIN_8, GPIO_PIN_RESET);
}

// input 캡처 콜백 함수
void HAL_TIM_IC_CaptureCallback(TIM_HandleTypeDef *htim)
{
  if (htim->Instance == TIM4)
  {
    if (htim->Channel == HAL_TIM_ACTIVE_CHANNEL_1)  // 전방 Echo
    {
      if (is_first_captured_front == 0)
      {
        ic_val1_front = HAL_TIM_ReadCapturedValue(htim, TIM_CHANNEL_1);
        __HAL_TIM_SET_CAPTUREPOLARITY(htim, TIM_CHANNEL_1, TIM_INPUTCHANNELPOLARITY_FALLING);
        is_first_captured_front = 1;
      }
      else
      {
        ic_val2_front = HAL_TIM_ReadCapturedValue(htim, TIM_CHANNEL_1);
        __HAL_TIM_SET_CAPTUREPOLARITY(htim, TIM_CHANNEL_1, TIM_INPUTCHANNELPOLARITY_RISING);
        __HAL_TIM_DISABLE_IT(htim, TIM_IT_CC1);
        uint32_t diff = (ic_val2_front > ic_val1_front) ? (ic_val2_front - ic_val1_front) : (0xFFFF - ic_val1_front + ic_val2_front);
        distance_front = (diff * 0.0343f) / 2.0f;
        is_first_captured_front = 0;
        __HAL_TIM_ENABLE_IT(htim, TIM_IT_CC1);
      }
    }

    else if (htim->Channel == HAL_TIM_ACTIVE_CHANNEL_2)  // 후방 Echo ← 수정됨
    {
      if (is_first_captured_rear == 0)
      {
        ic_val1_rear = HAL_TIM_ReadCapturedValue(htim, TIM_CHANNEL_2);
        __HAL_TIM_SET_CAPTUREPOLARITY(htim, TIM_CHANNEL_2, TIM_INPUTCHANNELPOLARITY_FALLING);
        is_first_captured_rear = 1;
      }
      else
      {
        ic_val2_rear = HAL_TIM_ReadCapturedValue(htim, TIM_CHANNEL_2);
        __HAL_TIM_SET_CAPTUREPOLARITY(htim, TIM_CHANNEL_2, TIM_INPUTCHANNELPOLARITY_RISING);
        __HAL_TIM_DISABLE_IT(htim, TIM_IT_CC2);
        uint32_t diff = (ic_val2_rear > ic_val1_rear) ? (ic_val2_rear - ic_val1_rear) : (0xFFFF - ic_val1_rear + ic_val2_rear);
        distance_rear = (diff * 0.0343f) / 2.0f;
        is_first_captured_rear = 0;
        __HAL_TIM_ENABLE_IT(htim, TIM_IT_CC2);
      }
    }
  }
}
```
- 전역변수 
    - 전방/후방 초음파 센서 각각에 대해 측정값 2개(IC1, IC2)와 캡처 상태 플래그 사용
    - 거리 계산 결과는 각각 distance_front, distance_rear에 저장됨
    - volatile: 인터럽트에 의해 변경되므로 최적화 방지

- `delay_us()` 함수
    - 타이머(TIM2)의 카운터를 사용한 마이크로초 지연 함수
    - Trigger 핀에 정확한 10us 펄스를 생성하기 위해 사용됨

- `Ultrasonic_Init()` 함수
    - TIM2: delay용 타이머 → 기본 카운터만 시작
    - TIM4: Echo 신호를 측정할 타이머 → CH1(전방), CH2(후방) 인터럽트 입력 캡처 시작

- `Ultrasonic_Trigger()` 함수
    - 전방(PA9), 후방(PA8) Trigger 핀에 10us HIGH 펄스를 각각 출력
    - 초음파 센서가 Echo 신호를 반환할 수 있도록 유도

- `HAL_TIM_IC_CaptureCallback()` 함수
    - Echo 핀에서 수신된 신호의 Rising/Falling 엣지를 인터럽트로 감지하고 처리
    - 전방: TIM_CHANNEL_1, 후방: TIM_CHANNEL_2
    - 작동 순서:
    1. Rising Edge: 시작 시간(ic_val1_*) 저장, 이후 Falling으로 폴라리티 전환
    2. Falling Edge: 끝 시간(ic_val2_*) 저장 후 다시 Rising으로 설정
    3. 시간 차(diff)를 기반으로 거리 계산:
        ```c
        //왕복이므로 2로 나눔
        // 초음파 속도: 343m/s → 0.0343 cm/us
        distance = (diff * 0.0343f) / 2.0f; 
        ```
    4. 인터럽트 잠시 끈 후 다시 활성화 (DISABLE_IT → ENABLE_IT)

### `main.c` 의 개선

기존(v1.5.0)의 main.c는 초음파 센서 제어, 거리 계산, 트리거 출력, CAN 송신 설정 및 전송까지 모든 로직이 하나의 파일에 집중되어 있었다.

각각의 동작이 main 함수 내에서 직접 수행되어 복잡하고 비직관적이며, 수정이나 확장 시 전체 로직에 영향을 주는 구조였다.

v1.6.0에서는 기능을 명확히 구분하여 모듈화(MVC 스타일 분리) 하였으며, main.c는 단순히 시스템 흐름을 제어하는 역할로만 구성되었다:

```c
while (1)
{
    if (HAL_GetTick() - prev_tick >= 100)
    {
        prev_tick = HAL_GetTick();

        Ultrasonic_Trigger();

        TxData[0] = (distance_front <= 10 || distance_rear <= 10) ? 1 : 0;

        CAN_Send();
    }
}

```

- Trigger 출력, 거리 계산은 ultrasonic.c에서 처리
- CAN 헤더 구성 및 송신은 can_handler.c에서 수행
- main은 단지 주기 체크 + 상태 확인 + 전송 명령만 담당

이로 인해 얻는 이점은 다음과 같다:
- 가독성 향상: main 함수는 시스템의 흐름만 담당하며, 각 기능은 독립된 모듈로 분리되어 로직이 명확하고 직관적으로 읽을 수 있다.

- 유지보수 용이: 오류 발생 시 해당 기능의 모듈만 점검하면 되므로, 디버깅 시간이 단축되고 안정성이 높아진다.

- 확장성 증가: 새로운 센서, 통신 방식(CAN 외 RF 등), 또는 기능 추가 시 기존 구조를 건드리지 않고 새로운 모듈만 추가하면 되므로, 프로젝트가 커져도 구조를 유지할 수 있다.

- 재사용성 강화: ultrasonic.c, can_handler.c 등은 다른 프로젝트에서도 그대로 활용 가능하여 개발 효율이 증가한다.

- 실시간성 확보 준비: 로직이 분리되어 있으므로, FreeRTOS 같은 RTOS 환경으로 쉽게 이식할 수 있는 기반이 된다.

이러한 개선은 단순한 코드 정리를 넘어 시스템의 품질과 확장 가능성 전반을 끌어올리는 핵심 구조적 변화라 할 수 있다.

---

## 향후 확장 방향: RTOS 도입을 통한 시스템 고도화

현재 Sensor ECU는 while(1) 기반의 순차 처리(Superloop) 구조로 동작하고 있다. 이는 초음파 센서 트리거, 엔코더 RPM 계산, CAN 데이터 전송 등 모든 로직이 단일 흐름 안에서 순서대로 실행됨을 의미한다.
앞으로 시스템의 실시간성, 확장성, 안정성을 획기적으로 향상시키기 위해 FreeRTOS 도입을 목표로 시스템 구조를 고도화할 예정이다.

### RTOS 도입의 필요성 및 기대 효과
현재 구조는 다음과 같은 순차 흐름을 따른다:
1. 일정 주기로 초음파 트리거 신호 출력
2. 입력 캡처 인터럽트에서 거리 계산
3. 거리 조건에 따라 CAN 데이터 설정
4. CAN 메시지 전송

이처럼 단일 루프에서 타이밍 기반으로 모든 기능을 수행하고 있으며,
기능이 추가될수록 타 작업 간 간섭, 우선순위 문제 등이 발생할 수 있다.

### RTOS 적용 시 기대 효과
- 실시간성 향상
    - 센서 데이터 수집과 CAN 전송 로직을 독립적인 Task 단위로 분리할 것이다.
    - **SensorTask**는 오직 10ms 주기에 맞춰 데이터를 정밀하게 수집하는 역할만 수행하고, **CANTask**는 데이터가 준비되었을 때만 깨어나 전송을 담당하게 된다.
    - 시간에 가장 민감한 SensorTask에 높은 우선순위를 부여하여 다른 작업에 의해 데이터 수집 주기가 밀리는 현상을 원천적으로 방지할 것이다.

- 시스템 확장성 향상
	- 향후 자가 진단, 상태 모니터링 등 새로운 기능이 추가될 때, 기존 로직을 수정할 필요 없이 새로운 태스크만 추가하면 되므로 구조적으로 깔끔하게 확장이 가능하다.
 	- 태스크 간 데이터는 **메시지 큐(Message Queue)**를 통해 안전하게 전달하여 데이터의 흐름을 명확히 하고, 인터럽트와 태스크가 공유하는 자원은 **크리티컬 섹션(Critical Section)**으로 보호하여 데이터 충돌 없이 안정적인 동작을 보장할 것이다. 

### 단계별 RTOS 적용 계획
- 1단계: 기능 분리 및 태스크화
	- `SensorTask`: 10ms의 정밀한 주기로 깨어나 초음파 센서를 트리거하고, 엔코더 값을 읽어 RPM을 계산한 뒤, 측정된 모든 데이터를 종합하여 내부 데이터 구조체에 저장하는 역할을 맡길 것이다.
	- `CANTask`: SensorTask가 측정을 마친 데이터를 읽어와 CAN 프로토콜 형식에 맞게 가공하고(e.g., 거리→비트마스크, RPM→2바이트 분리), 이를 전송하는 역할만 전담하도록 할 것이다.

- 2단계: 태스크 간 통신 구조 적용
	- SensorTask가 측정한 최종 데이터 패킷(SensorData_t)을 **메시지 큐(Message Queue)**를 사용해 CANTask로 전달하는 구조를 적용할 것이다.
 	- 이러한 이벤트 기반 구조를 통해 CANTask는 데이터가 있을 때만 동작하므로 CPU 자원을 효율적으로 사용하고, 두 태스크의 동작이 완벽히 분리(Decoupling)되어 시스템의 예측 가능성과 디버깅 용이성이 향상될 것이다.

- 3단계: 자원 보호 적용
	- 초음파 거리 값처럼 인터럽트 서비스 루틴(ISR)과 SensorTask가 공유하는 데이터에 대해서는, 데이터 읽기/쓰기 도중 충돌이 발생하지 않도록 **크리티컬 섹션(Critical Section)**으로 보호하여 데이터 무결성을 확보할 계획이다.
 	 이를 통해 태스크가 데이터를 읽는 도중에 인터럽트가 발생하여 값이 변경되는 위험을 방지할 것이다.

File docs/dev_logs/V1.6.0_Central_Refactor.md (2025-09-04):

# Central 부 파일 분할 및 코드 최적화, CAN 개선 (v1.6.0)

## 파일 분할 및 코드 최적화 목적

기존 central_v1.5.0은 모든 기능이 main.c 파일 하나에 집중되어 코드의 복잡도가 높고 유지보수가 어려웠다. 이를 해결하기 위해 v1.6.0에서는 RF 통신, 모터 제어, CAN 통신 로직을 각각의 독립적인 파일로 분리하여 모듈화했다. 이러한 구조 개선은 코드의 가독성과 재사용성을 높이고, 각 기능의 독립성을 확보하여 향후 기능 추가나 수정이 용이한 확장 가능한 구조를 만들기 위함이며, 특히 CAN 수신 데이터가 RF 통신으로 전달되는 과정을 명확히 하여 시스템 전체의 안정성과 신뢰도를 향상시키기 위한 목적이다.

---

## 주요 변경 사항

### 1. 파일 분할 (모듈화)

기존 `main.c`의 역할을 분산시키고, 기능별 독립성을 확보하기 위해 아래와 같이 파일을 분할함

- `can_handler.c/.h` (CAN 통신 핸들러)
    - 역할: CAN 필터 설정, 수신 인터럽트 처리, 수신 데이터의 거리 판단(위험/안전) 신호를 내부 상태 변수(can_distance_signal)에 저장하며, 해당 신호를 햅틱 제어 및 RF ACK 응답에 활용함.

    - 주요 함수 : `CANHandler_Init()` : CAN 시작 및 필터 초기화, `CAN_Filter_Config()` : 0x6A5 ID에 대한 필터 설정, `HAL_CAN_RxFifo1MsgPendingCallback()` : 수신된 거리 신호에 따라 햅틱 출력 및 상태 변수 업데이트

- `rf_handler.c/.h` (RF 통신 핸들러)
    - 역할 : 컨트롤러에서 수신된 주행 명령 패킷(Roll, Accel, Brake, 방향)을 파싱하고, CAN 수신 신호를 ACK 페이로드로 회신하여 핸들 상태에 반영되도록 처리함.

    - 주요 함수 : `RFHandler_Init()` : NRF24 수신 모드 초기화, `RFHandler_IrqCallback()` : EXTI 인터럽트 발생 시 수신 처리 준비, `RFHandler_GetNewCommand()` : 새로운 명령이 수신되었는지 확인 후 파싱하여 반환, `RFHandler_SetAckPayload()` : CAN 수신 거리 신호를 다음 ACK에 포함하도록 설정

- `motor_control.c/h` (모터 제어 모듈)
    - 역할 : RF에서 수신한 주행 명령에 따라 DC 모터와 서보 모터를 제어하며, 엔코더를 기반으로 실시간 RPM을 측정함. 속도 피드백은 외부 출력 또는 디버깅용으로 활용 가능.

    - 주요 함수 : `MotorControl_Init()` : PWM 및 엔코더 타이머 시작, 기본 방향 설정, `MotorControl_Update()` : roll, accel, brake, 방향에 따라 서보/DC 모터 제어 수행, `MotorControl_GetRPM()` : 주기적으로 계산된 현재 DC 모터 RPM 반환

- `main.c`의 역할 변경
    - 역할 : 초기화 이후 main() 루프에서 각 핸들러의 업데이트 함수들을 순차적으로 호출하는 중재자(Coordinator) 역할을 수행하며, 복잡한 제어/통신 로직은 전부 can_handler, rf_handler, motor_control로 위임됨.

### 2. 코드 구조 최적화

파일 분할을 통해 아래와 같은 코드 구조 개선을 진행하였다.

#### 데이터 흐름 명확화
- 내용: 
    - 컨트롤러에서 수신한 주행 명령은 VehicleCommand_t 구조체로 파싱되며, rf_handler 모듈 내에서 생성되어 motor_control로 전달된다.

    - 거리 감지 결과는 can_handler에서 수신된 값을 can_distance_signal 전역 변수로 저장하고, 이 값을 rf_handler에서 ACK 페이로드로 전송한다.

- 효과 : 모든 데이터가 명확한 흐름(→ 구조체 또는 상태 변수 → 다른 모듈의 함수 호출)을 따르므로 전역 변수의 혼용을 최소화하고, 데이터 추적이 직관적으로 가능해짐

#### 캡슐화 및 책임 분리
- 내용 : 
    - main.c는 더 이상 RF 버퍼, CAN 수신 패킷, 모터 PWM 값 등의 내부 세부 사항을 다루지 않는다.

    - 각 모듈은 자신이 담당하는 작업만 수행하고, 필요한 인터페이스 함수만 외부에 노출

        - 예: RFHandler_GetNewCommand()는 새 명령이 도착했는지만 알려주고, 파싱된 데이터를 반환
        - MotorControl_Update()는 받은 명령 구조체에 따라 내부 로직으로 모터 상태를 제어

- 효과 : 모듈 간 결합도가 낮아져 유지보수와 테스트가 쉬워지고, 코드 수정 시 다른 파일에 미치는 영향도 최소화

### 3. 주요 개선 사항: 통신 성능 최적화

v1.6.0에서는 사용자 조작에 대한 반응성을 크게 향상시키기 위해 RF 통신과 CAN 통신 모두에서 성능 최적화를 적용하였다. 이를 통해 End-to-End 지연 시간을 최소화하고, 조작에 대한 반응이 거의 실시간처럼 느껴질 수 있도록 개선하였다.

#### RF 통신 최적화
1. 데이터 송신 속도 향상
    - NRF24L01의 전송 속도를 기존 1Mbps → 2Mbps로 설정하여, 물리적인 전송 시간을 절반으로 단축.

2. 데이터 패킷 크기 최적화
    - 실제 사용하는 명령만 포함되도록 데이터 패킷 구조를 정리하여, 32바이트 → 8바이트로 축소.
    - 전송 시간 감소 + 버퍼 오버플로우 방지 + 응답 속도 향상.

#### CAN 통신 최적화
1. 보드레이트 향상
    - CAN의 Prescaler 값을 72 → 18로 조정하여, 125kbps → 500kbps의 고속 통신 환경으로 개선.
    - 더 짧은 시간에 메시지를 전송할 수 있어 거리 감지와 햅틱 응답의 딜레이가 감소.

2. 자동 재전송 및 오류 복구 기능 활성화
    - AutoBusOff와 AutoRetransmission 기능을 활성화하여, 일시적인 에러 상황에서도 자동으로 CAN 버스 복귀 및 재전송 수행.
    - 수동 복구 처리 없이 안정적인 실시간 통신을 보장.

3. 수신 ID와 데이터 길이 검증을 통한 유효성 강화
    - CAN 수신 콜백 함수(HAL_CAN_RxFifo1MsgPendingCallback)에서 수신된 메시지의 StdId와 DLC(Data Length Code)를 확인하여, 정확히 0x6A5 ID이며 데이터 길이가 1바이트일 때만 유효한 데이터로 처리하도록 구현.
    - 이를 통해 의도치 않은 메시지 처리로 인한 오동작을 예방하고, 중요한 거리 신호만을 반영함으로써 시스템의 안정성과 응답성을 향상시킴.
    - 특히 브로드캐스트 환경 또는 다중 노드 통신에서 ID 매칭 기반 필터링과 별개로 소프트웨어 레벨의 2차 검증 역할을 수행함.

#### 개선 효과

- End-to-End 지연 시간 최소화: RF → 중앙 MCU → CAN 수신 노드까지의 통신 흐름이 전반적으로 최적화되어, 컨트롤러 조작 시 햅틱 피드백이나 차량 응답이 즉시 반영되는 체감 반응성을 실현.

- 시스템 안정성 향상: 에러 상황에서도 자동 복구 기능이 동작하여, 조작 중 통신 끊김 없이 지속적인 운용 가능성 확보.

- 성능 기반 확장성 확보: 고속 통신 기반 구조를 통해 센서 추가, 다중 노드 통신 확장에도 대응할 수 있는 기반을 마련.

---

## 주요 코드 설명

### `can_handler.h`: CAN 통신 모듈 인터페이스 정의
```c
#ifndef INC_CAN_HANDLER_H_
#define INC_CAN_HANDLER_H_

#include "main.h"

// =============================
// CAN 수신 메시지 설명:
// ID 0x6A5, RxData[0] = 거리 조건 (1: 위험, 0: 안전)
// =============================

// ▶ 외부에서 접근할 수 있는 변수들
extern CAN_FilterTypeDef sFilterConfig;
extern CAN_RxHeaderTypeDef RxHeader;
extern uint8_t RxData[8];
extern volatile uint8_t can_distance_signal;

// ▶ 초기화 함수: CAN 시작 및 필터 설정
void CANHandler_Init(void);

// ▶ 필터 설정 함수: 특정 ID 수신 설정
void CAN_Filter_Config(CAN_HandleTypeDef *hcan_ptr);

// ▶ 수신 인터럽트 콜백 함수 (FIFO1 사용)
void HAL_CAN_RxFifo1MsgPendingCallback(CAN_HandleTypeDef *hcan);

#endif /* INC_CAN_HANDLER_H_ */
```
- can_distance_signal: 거리 조건(위험 여부)을 저장해 다른 모듈(RF 등)에서 사용할 수 있도록 함
- HAL_CAN_RxFifo1MsgPendingCallback: CAN 수신 인터럽트에 의해 자동 호출됨

### `can_handler.c`: CAN 통신 모듈 구현
```c
#include "can_handler.h"
#include "can.h" // hcan 정의가 여기에 있을 수 있습니다.

// =============================
// CAN 수신(Rx) 패킷 구조 정의
// -----------------------------
// ▶ CAN 수신 ID:
//   - StdId: 0x6A5 (슬레이브 → 마스터)
//   - 필터 모드: 11비트 표준 ID, 마스크 0x7FF (전비트 일치)
// ▶ 수신 헤더 (RxHeader):
//   - RxHeader.StdId : 송신 측 ID 확인용 (0x6A5 expected)
//   - RxHeader.DLC   : 데이터 길이 (보통 1)
// ▶ 수신 데이터 (RxData):
//   - RxData[0] : 거리 조건 결과 (uint8_t, 거리값에따라 1 or 0 수신)
//   - RxData[1] ~ RxData[7] : 예비, 현재 미사용
// =============================

CAN_FilterTypeDef sFilterConfig;
CAN_RxHeaderTypeDef RxHeader;
uint8_t RxData[8];
volatile uint8_t can_distance_signal = 0;

void CANHandler_Init(void)
{
	extern CAN_HandleTypeDef hcan;
	HAL_CAN_Start(&hcan);
	CAN_Filter_Config(&hcan);
}

// can 필터 설정 및 인터럽트 활성화 함수
void CAN_Filter_Config(CAN_HandleTypeDef *hcan_ptr)
{
   // Configure the filter
   sFilterConfig.FilterActivation = CAN_FILTER_ENABLE;
   sFilterConfig.FilterFIFOAssignment = CAN_FILTER_FIFO1;
   sFilterConfig.FilterMode = CAN_FILTERMODE_IDMASK;
   sFilterConfig.FilterIdHigh = 0x6A5<<5;
   sFilterConfig.FilterIdLow = 0;
   sFilterConfig.FilterMaskIdHigh = 0x7FF<<5; // SET 0 to unfilter
   sFilterConfig.FilterMaskIdLow = 0;
   sFilterConfig.FilterScale = CAN_FILTERSCALE_32BIT;

   if (HAL_CAN_ConfigFilter(&hcan, &sFilterConfig) != HAL_OK)
           Error_Handler(); // 실패 시 무한 루프 등 처리

   // Activate the notification
   if (HAL_CAN_ActivateNotification(&hcan, CAN_IT_RX_FIFO1_MSG_PENDING) != HAL_OK)
           Error_Handler(); // 실패 시 처리
}

// CAN 수신 인터럽트 콜백 함수 (FIFO1)
void HAL_CAN_RxFifo1MsgPendingCallback(CAN_HandleTypeDef *hcan)
{
  HAL_CAN_GetRxMessage(hcan, CAN_RX_FIFO1, &RxHeader, RxData);

  // 수신 ID와 데이터 길이 확인
  if (RxHeader.StdId == 0x6A5 && RxHeader.DLC == 1)
  {
	  // 거리 상태(0 또는 1)를 내부 변수에 저장
	  can_distance_signal = RxData[0];
  }
}
```
1. CAN 필터 설정 – 정밀 수신 필터링 (ID 0x6A5 고정 수신)
    - CAN_Filter_Config() 함수는 STM32의 ID 마스크 필터 방식 (IDMASK)을 활용하여 0x6A5 ID만 수신 허용.
    - 필터 마스크 0x7FF << 5로 11비트 전비트 일치 조건을 설정 → 다른 메시지는 하드웨어 레벨에서 차단됨.
    - 수신 대상 메시지는 FIFO1으로 설정되며, 해당 FIFO에 데이터가 도착하면 수신 인터럽트 자동 발생.
    - 목적:
        - 초음파 거리 감지용 CAN 메시지(0x6A5)만 선별적으로 처리하여 통신 효율과 안정성 향상.
        - 불필요한 소프트웨어 검사 없이 하드웨어 필터링으로 CPU 부하 최소화.

2. CAN 수신 인터럽트 처리 – Rx FIFO1 기반, 실시간 응답 구조
    - HAL_CAN_RxFifo1MsgPendingCallback() 함수는 FIFO1 수신 시 자동 호출되는 인터럽트 핸들러.
    - 내부에서 HAL_CAN_GetRxMessage()로 수신 데이터를 읽은 후, 다음 조건을 검사:
        - RxHeader.StdId == 0x6A5
        - RxHeader.DLC == 1
    - 조건이 일치하면 RxData[0]에 저장된 거리 감지 결과 (0 또는 1) 값을 전역 변수 can_distance_signal에 저장.
    - 목적:
        - 초음파 거리 감지 결과를 즉시 햅틱 출력/경고에 반영.
        - can_distance_signal은 RF 응답 페이로드, OLED 표시, 로직 판단 등에 참조됨.
        - 조건 불일치 시 무시 처리 → 데이터 유효성 검증 강화.

3. 모듈 초기화 – 통신 시작과 인터럽트 설정 통합 처리
    - CANHandler_Init() 함수는 다음 세 가지 초기화 절차를 일괄 수행:
        - HAL_CAN_Start() : CAN 동작 시작
        - CAN_Filter_Config() : ID 필터 등록 및 FIFO 지정
        - HAL_CAN_ActivateNotification() : FIFO1 수신 인터럽트 활성화
    - 목적:
        - 메인 루프에서 CAN 수신을 직접 폴링하지 않아도 되는 비동기 이벤트 기반 구조 구성.
        - 시스템 부팅 시 자동으로 통신이 준비되며, 완전한 자동 수신-처리 체계 구현

### `rf_handler.h`: RF 통신 모듈 인터페이스 정의
```c
#ifndef INC_RF_HANDLER_H_
#define INC_RF_HANDLER_H_

#include "main.h"
#include <stdbool.h>

// ▶ 수신된 주행 명령 데이터를 담는 구조체
typedef struct {
    float roll;
    uint16_t accel_ms;
    uint16_t brake_ms;
    uint8_t direction;
} VehicleCommand_t;

// ▶ NRF24 초기화 (수신모드 설정)
void RFHandler_Init(void);

// ▶ EXTI 인터럽트 발생 시 호출 (nRF IRQ 핀)
void RFHandler_IrqCallback(void);

// ▶ 다음 ACK 페이로드 데이터를 설정 (e.g. can_distance_signal)
void RFHandler_SetAckPayload(uint8_t signal);

// ▶ 새로운 주행 명령 수신 여부 확인 및 파싱
bool RFHandler_GetNewCommand(VehicleCommand_t* command);

#endif /* INC_RF_HANDLER_H_ */
```
- 외부에서 사용할 수 있는 초기화 함수, IRQ 콜백, ACK 설정 및 수신 명령 파싱 기능이 선언되어 있음

### `rf_handler.c`: RF 통신 모듈 구현
```c
#include "rf_handler.h"
#include "NRF24.h"
#include "NRF24_reg_addresses.h"
#include <string.h>

// ▶ 페이로드 크기 정의
#define RX_PAYLOAD_SIZE 8
#define ACK_PAYLOAD_SIZE 2

// ▶ 내부 상태 변수
static volatile uint8_t nrf_irq_flag = 0;             // IRQ 발생 여부
static uint8_t ack_response[ACK_PAYLOAD_SIZE] = {0};  // 다음 전송할 ACK 페이로드

// ▶ NRF24 모듈 초기화 (수신 전용)
void RFHandler_Init(void)
{
    static uint8_t rx_addr[5] = {0x45, 0x55, 0x67, 0x10, 0x21};

    csn_high(); HAL_Delay(5); ce_low();
    nrf24_init();
    nrf24_auto_ack_all(enable);
    nrf24_en_ack_pld(enable);       // ACK payload 활성화
    nrf24_dpl(disable);
    nrf24_set_crc(enable, _1byte);
    nrf24_tx_pwr(_0dbm);
    nrf24_data_rate(_2mbps);        // 속도 설정
    nrf24_set_channel(90);
    nrf24_set_addr_width(5);
    nrf24_open_rx_pipe(1, rx_addr);
    nrf24_pipe_pld_size(1, RX_PAYLOAD_SIZE);
    nrf24_listen();
}

// ▶ 외부 인터럽트 핸들러에서 호출되는 콜백
void RFHandler_IrqCallback(void)
{
    nrf_irq_flag = 1;
}

// ▶ 다음 ACK 페이로드 설정 함수
void RFHandler_SetAckPayload(uint8_t signal)
{
    ack_response[0] = signal;  // can_distance_signal 등 설정
}

// ▶ 새 데이터 수신 여부 확인 및 명령 파싱
bool RFHandler_GetNewCommand(VehicleCommand_t* command)
{
    if (!nrf_irq_flag) return false;

    nrf_irq_flag = 0;
    uint8_t status = nrf24_r_status();

    if (status & (1 << RX_DR))
    {
        uint8_t rx_buffer[RX_PAYLOAD_SIZE] = {0};
        nrf24_receive(rx_buffer, RX_PAYLOAD_SIZE);

        // ACK 페이로드 응답 전송
        nrf24_transmit_rx_ack_pld(1, ack_response, ACK_PAYLOAD_SIZE);
        nrf24_clear_rx_dr();

        if (rx_buffer[0] == 1) // 주행 명령
        {
            int16_t roll_encoded;
            memcpy(&roll_encoded, &rx_buffer[1], sizeof(int16_t));
            command->roll = ((float)roll_encoded) / 100.0f;

            memcpy(&command->accel_ms, &rx_buffer[3], sizeof(uint16_t));
            memcpy(&command->brake_ms, &rx_buffer[5], sizeof(uint16_t));
            command->direction = rx_buffer[7];

            return true;
        }
    }

    return false;
}
```

- NRF24 수신 초기화
    - RFHandler_Init()은 NRF24L01을 수신 모드로 설정하고, 자동 응답(ACK) + 페이로드 포함 전송 기능을 활성화한다.
    - 데이터 레이트 2Mbps, 채널 90, 주소 폭 5바이트, 파이프 1번 사용 등 실시간 제어에 최적화된 설정이 적용된다.
    - 목적: 컨트롤러와의 고속 양방향 통신을 위한 하드웨어 설정

- 인터럽트 기반 비동기 수신
    - EXTI 인터럽트가 발생하면 nrf_irq_flag를 세팅하여 메인 루프나 작업자 함수가 비동기적으로 수신 처리를 할 수 있도록 설계
    - 목적: 폴링이 아닌 인터럽트 기반 수신 처리 → CPU 점유율 최소화

- 주행 명령 파싱 및 구조화
    - rx_buffer에서 받은 바이트를 해석하여 VehicleCommand_t 구조체로 변환
        - roll (int16 → float 변환)
        - accel_ms, brake_ms, direction
    - 목적: 실수 없이 정형화된 주행 명령 데이터로 모터 제어 모듈에 직접 전달 가능

- ACK 페이로드 기반 상태 응답
    - RF 수신 시 nrf24_transmit_rx_ack_pld()를 통해 즉시 ACK 페이로드 전송.
    - can_handler에서 받은 can_distance_signal을 사전에 ack_response[0]에 담아 사용.
    - 목적: 컨트롤러에서 즉시 거리 상태 확인 가능, 햅틱 피드백 동기화

### `motor_control.h` : 모터 제어 모듈 인터페이스
```c
#ifndef INC_MOTOR_CONTROL_H_
#define INC_MOTOR_CONTROL_H_

#include "main.h"
#include "rf_handler.h" // VehicleCommand_t 사용을 위해 포함

/**
 * @brief 모든 모터 관련 주변장치(PWM, 방향핀, 엔코더 등) 초기화
 */
void MotorControl_Init(void);

/**
 * @brief 수신된 주행 명령에 따라 서보 및 DC모터를 제어
 * @param command: roll, accel, brake, direction 정보를 담은 구조체
 */
void MotorControl_Update(const VehicleCommand_t* command);

/**
 * @brief 현재 DC 모터의 RPM을 반환
 */
float MotorControl_GetRPM(void);

#endif /* INC_MOTOR_CONTROL_H_ */
```
- DC 모터 및 서보 모터의 제어 기능을 외부에 제공하며, 주행 명령 구조체(VehicleCommand_t) 기반 제어 함수 및 RPM 측정 함수가 선언되어 있다.

### `motor_control..c`: 모터 제어 모듈 구현
```c
#include "motor_control.h"
#include <math.h> // fabsf

// 타이머 외부 참조 (STM32CubeMX에서 생성된 핸들 사용)
extern TIM_HandleTypeDef htim1; // DC 모터 PWM
extern TIM_HandleTypeDef htim2; // 서보 모터 PWM
extern TIM_HandleTypeDef htim4; // 엔코더 입력

// 내부 설정 변수
static TIM_HandleTypeDef* dc_motor_htim = &htim1;
static uint32_t dc_motor_channel = TIM_CHANNEL_4;

static TIM_HandleTypeDef* servo_htim = &htim2;
static uint32_t servo_channel = TIM_CHANNEL_3;

static float motor_rpm = 0.0f;

// === RPM 계산용 매크로 및 상수 ===
#define PPR 11
#define GEAR_RATIO 21.3f
#define TICKS_PER_REV (PPR * GEAR_RATIO * 4)

// 모터 방향 전환 매크로
#define MOTOR_FORWARD()  do { HAL_GPIO_WritePin(GPIOA, GPIO_PIN_0, GPIO_PIN_RESET); HAL_GPIO_WritePin(GPIOA, GPIO_PIN_1, GPIO_PIN_SET); } while(0)
#define MOTOR_BACKWARD() do { HAL_GPIO_WritePin(GPIOA, GPIO_PIN_0, GPIO_PIN_SET); HAL_GPIO_WritePin(GPIOA, GPIO_PIN_1, GPIO_PIN_RESET); } while(0)

typedef enum {
    DIRECTION_BACKWARD = 0,
    DIRECTION_FORWARD  = 1
} MotorDirection_t;

// === 초기화 함수 ===
void MotorControl_Init(void)
{
    HAL_TIM_PWM_Start(dc_motor_htim, dc_motor_channel);
    HAL_TIM_PWM_Start(servo_htim, servo_channel);
    HAL_TIM_Encoder_Start(&htim4, TIM_CHANNEL_ALL);
    MOTOR_FORWARD(); // 기본 방향
}

// === 전체 명령 기반 제어 함수 ===
void MotorControl_Update(const VehicleCommand_t* command)
{
    Update_Motor_RPM();
    Update_MotorDirection((MotorDirection_t)command->direction);
    Control_Servo(command->roll);
    Control_DcMotor(command->accel_ms, command->brake_ms);
}

// === 현재 RPM 반환 함수 ===
float MotorControl_GetRPM(void)
{
    return motor_rpm;
}

// === 내부 전용 함수 ===

static void Update_Motor_RPM(void)
{
    static int16_t last_encoder = 0;
    static uint32_t last_tick = 0;
    uint32_t now = HAL_GetTick();

    if (now - last_tick >= 100) // 100ms 주기
    {
        last_tick = now;
        int16_t enc = (int16_t)__HAL_TIM_GET_COUNTER(&htim4);
        int16_t delta = enc - last_encoder;
        last_encoder = enc;

        motor_rpm = fabsf(((float)delta / TICKS_PER_REV) * 10.0f * 60.0f);
    }
}

static void Control_Servo(float roll)
{
    if (roll < -90.0f) roll = -90.0f;
    if (roll >  90.0f) roll =  90.0f;
    float angle = roll + 90.0f;
    uint16_t pwm = (uint16_t)(1200 + (angle / 180.0f) * (1900 - 1200));
    __HAL_TIM_SET_COMPARE(servo_htim, servo_channel, pwm);
}

static void Control_DcMotor(uint16_t accel_ms, uint16_t brake_ms)
{
    static int16_t duty = 0;
    const int16_t accel_step = 50;
    const int16_t brake_step = 100;
    const int16_t max_duty = 1000;

    if (brake_ms > 0) duty -= brake_step;
    else if (accel_ms > 0) {
        if (duty == 0) duty = 300;
        duty += accel_step;
    } else {
        duty -= accel_step;
    }

    if (duty < 0) duty = 0;
    if (duty > max_duty) duty = max_duty;
    __HAL_TIM_SET_COMPARE(dc_motor_htim, dc_motor_channel, duty);
}

static void Update_MotorDirection(MotorDirection_t direction)
{
    static MotorDirection_t prev = DIRECTION_FORWARD;
    if (direction != prev) {
        prev = direction;
        if (direction == DIRECTION_FORWARD) MOTOR_FORWARD();
        else MOTOR_BACKWARD();
    }
}
```
- PWM 기반 제어
    - 서보 모터: roll 값을 -90° +90° 범위로 매핑 → 1200 1900us PWM 출력
    - DC 모터: PWM duty 비율을 accel_ms, brake_ms에 따라 가감속 제어
    - 목적: 사용자 입력에 따라 정밀한 속도 및 조향 제어

- DC 모터 방향 제어 (GPIO)
    - IN1/IN2 핀을 이용한 정/역회전 제어 (MOTOR_FORWARD(), MOTOR_BACKWARD() 매크로)
    - 이전 방향 상태와 비교 후 변경 시에만 핀 전환
    - 목적: 방향 전환 시 노이즈 및 급격한 반전 방지

- 엔코더 기반 실시간 RPM 측정
    - 100ms 주기로 엔코더 카운터 변화량 계산 → 기어비와 PPR 고려하여 RPM 산출
    - fabsf()를 통해 항상 양수 출력
    - 목적: 속도 피드백 기반 향후 PID 제어 등 확장 기반 마련

- 명령 구조체 기반 전체 제어 통합
    - MotorControl_Update() 함수는 외부에서 받은 VehicleCommand_t 구조체 하나만으로 전체 모터 상태(조향, 가감속, 방향)를 통합 제어
    - 목적: 외부 모듈과의 연계성을 높이고 코드 유지보수 간소화

### `main.c` 의 개선

이전의 main.c는 모든 기능이 한 파일에 집중되어 있었다. RF 수신, 데이터 파싱, 모터 제어, 방향 전환, CAN 응답 생성까지 모두 main() 함수 안에서 직접 처리했다. 구조가 복잡하고 가독성이 낮았으며, 유지보수나 기능 확장 시 전체 코드에 영향을 주기 쉬웠다.

반면 v1.6.0 구조에서는 이러한 책임을 모듈별로 분리했다. main() 함수는 다음과 같이 단순화되었다:

```c
while (1)
{
    if (RFHandler_GetNewCommand(&command))
    {
        MotorControl_Update(&command);
    }

    RFHandler_SetAckPayload(can_distance_signal);
}
```

이제 main.c는 RF로부터 명령을 받아 모터를 제어하고, 거리 상태를 응답에 포함하는 중재자 역할만 수행한다. 세부 로직은 rf_handler, motor_control, can_handler 등 각 파일에서 처리된다.

이로 인해 얻는 이점은 다음과 같다:

- 가독성 향상: 흐름이 단순하고 직관적이다.
- 유지보수 용이: 문제 발생 시 관련 모듈만 보면 된다.
- 확장성 증가: 새로운 기능을 별도 모듈로 추가하기 쉽다.

즉, v1.6.0은 기존의 복잡한 구조를 모듈화된 구조로 최적화하여, 실시간성·유지보수성·확장성을 모두 향상시켰다.

---

## 향후 확장 방향: RTOS 도입을 통한 시스템 고도화

v1.6.0에서 완성된 모듈화 구조는 while(1) 루프 기반의 순차적 처리 방식(Superloop)을 넘어,
실시간 운영체제(RTOS)를 도입하기 위한 훌륭한 기반이 되었다.
향후 시스템의 실시간성, 안정성, 확장성을 극대화하기 위해 FreeRTOS 도입을 목표로 한다.

### RTOS 도입의 필요성 및 기대 효과

현재 구조는 RF 수신, 모터 제어, CAN 통신 등 다양한 작업을 하나의 메인 루프에서 순차적으로 수행한다. 이 방식은 기능이 증가할수록 특정 작업이 다른 작업의 실행을 지연시키는 문제가 발생할 수 있다. RTOS를 도입하면 이러한 문제를 해결하고 다음과 같은 효과를 기대할 수 있다:

- 실시간 응답성 확보 : 시간에 민감한 작업(RF 명령 수신, 모터 제어)과 덜 민감한 작업(상태 전파)을 각각 독립적인 **태스크(Task)**로 분리하고 우선순위를 부여할 수 있다. 이를 통해 모터 제어가 다른 기능에 의해 지연되는 현상을 원천적으로 방지하고, 운전자의 조작에 즉각적으로 반응하는 시스템을 구현할 수 있다.

- 안정적인 동시 처리 : RF 수신과 CAN 수신처럼 언제 발생할지 모르는 비동기 이벤트들을 **세마포어(Semaphore)와 메시지 큐(Message Queue)**를 통해 효율적으로 처리할 수 있다. CPU가 불필요한 대기(Polling) 없이 이벤트를 처리하게 되어 시스템의 전반적인 효율과 안정성이 크게 향상된다.

- 시스템 확장성 향상 : 각 기능이 독립적인 태스크로 모듈화되어 있어, 향후 PID 제어, 데이터 로깅, 배터리 모니터링 등 새로운 기능을 추가할 때 기존 코드에 미치는 영향을 최소화하며 쉽게 시스템을 확장할 수 있다.

### 단계별 적용 계획

#### 1단계: 태스크 분리 및 우선순위 설계
시스템의 핵심 기능을 2개의 독립적인 FreeRTOS 태스크로 분리하여 전환할 계획이다.

- `RFTask` (높은 우선순위): 조종기 RF 명령 수신, 주행 명령 해석, 모터 제어, CAN 피드백 처리 등 시스템의 핵심 제어 로직을 총괄하는 태스크를 설계한다. 사용자 조작에 대한 즉각적인 반응을 보장하기 위해 가장 높은 우선순위를 할당할 것이다.

- `CANTask` (보통 우선순위): RFTask로부터 처리된 차량 상태를 전달받아 CAN 버스로 전파하는 게이트웨이 역할을 수행하는 태스크를 설계한다. 제어 자체보다 시간 제약이 덜 엄격하므로 보통 우선순위로 설정하여 핵심 제어 로직을 방해하지 않도록 한다.

#### 2단계: 태스크 간 통신 및 동기화 구조 변경
태스크 간 데이터 교환 및 이벤트 처리는 RTOS가 제공하는 안전하고 효율적인 메커니즘을 통해 구현할 것이다.

- **인터럽트 처리** : RF 수신 인터럽트는 **세마포어(RFSemHandle)**를 통해 RFTask를 즉시 깨우고, CAN 수신 인터럽트는 **메시지 큐(CANRxQueueHandle)**에 데이터를 직접 전송하여 RFTask에 안전하게 전달하는 구조를 적용한다.

- **태스크 간 통신**: RFTask는 처리된 주행 명령을 또 다른 **메시지 큐(CANTxQueueHandle)**에 전송하고, CANTask는 해당 큐로부터 데이터를 수신하여 처리하는 방식으로 두 태스크의 동작을 완벽히 분리할 계획이다.

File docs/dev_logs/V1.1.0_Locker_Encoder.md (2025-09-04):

#  코드 리팩토링 및 전/후진 기능, 모터 RPM 측정 로직 추가 (v1.1.0)

## 개선 및 기능 추가
- 핸들에 Locker 스위치를 추가하여, 스위치 토글 방향에 따라 차량 DC 모터의 회전 방향을 제어함으로써 전/후진 기능을 구현
- 이전에 구현한 DC 모터의 Timer Encoder 모드를 활용하여 모터 RPM을 측정 및 계산하는 로직을 추가
- v1.0.0의 코드를 로직별로 함수화하고 전반적인 구조를 리팩토링하여 가독성과 유지보수성을 향상

---

## 하드웨어 연결

### 송신부(Rx)
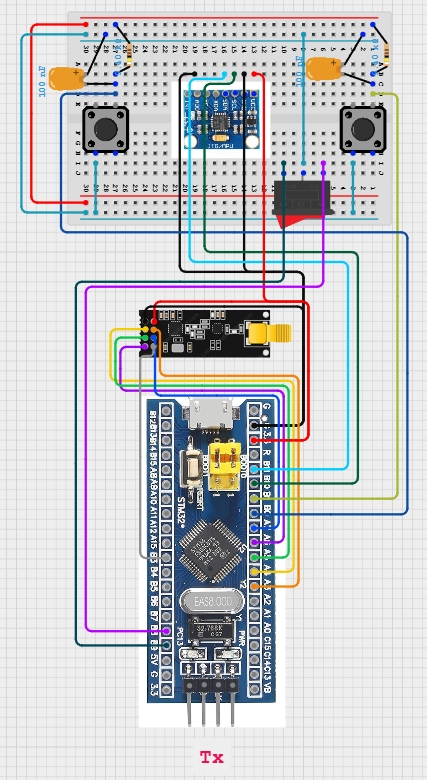
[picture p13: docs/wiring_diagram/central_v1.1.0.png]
Locker, Encoder RPM 측정 추가 배선도


※ 수신부(Rx)는 [V1.0.0_RF_MotorCtrl.md](./V1.0.0_RF_MotorCtrl.md)와 동일

---

## STM32CubeMX 설정

### 송신부 변경 사항
- Motor_Forward 
    - PB8 : GPIO_Input (Pull-Up)
- Motor_Backward 
    - PB9 : GPIO_Input (Pull-Up)

### 수신부 변경사항

DC모터 Encoder
- combined channels > encoder mode
- pb6 (tim4_ch1) : encoderA
- pb7 (tim4_ch2) : encoderB
- encoder mode TI1 adn TI2
- prescaler : 0
- Counter period(ARR) : 65535 or 0xFFFF (엔코더 overflow 방지)
- Counter Mode : UP
- IC1 Polarity: Rising Edge
- IC1 Selection: Direct TI
- IC1 Prescaler: No division (1번마다 1번 인식 = 모든 엣지를 다 인식함)
- IC1 Filter: 10 (노이즈가 심하면 값을 올려줘야함)
- (IC2 항목도 동일하게 설정)

> 참고 [V1.0.0_RF_MotorCtrl.md](./V1.0.0_RF_MotorCtrl.md)
---

## 동작 코드
다음은 기존의 v1.0.0 버전의 코드를 리팩토링한 사항을 요약한 것이다.

### 송신부(Tx)
#### 1. RF 송신 초기화 코드를 main에서 분리하여 NRF24_Tx_Init() 함수로 별도 정의
-> 유지보수/디버깅 시 어느 부분에서 문제가 발생했는지 빠르게 파악 가능
-> 향후 FreeRTOS Task화 또는 모듈별 재사용이 쉬움.

#### 2. NRF24 송신 데이터의 각 필드를 바이트 오프셋 기준으로 주석화
-> 통신 구조의 명확성을 높여 수신 파싱, 디버깅, 유지보수 및 확장에 용이.

```c
/* USER CODE BEGIN 0 */
// =============================
// NRF24 송신 패킷 구조 정의
// -----------------------------
// Byte 0   : 메시지 식별자 (1)
// Byte 1~2 : roll (int16_t, 센서 측에서 ×100 배율 인코딩)
// Byte 3~4 : accel_ms (uint16_t, 엑셀 유지 시간)
// Byte 5~6 : brake_ms (uint16_t, 브레이크 유지 시간)
// Byte 7   : direction (0: BACKWARD, 1: FORWARD)
// 나머지 Byte 8~31 : 예약 or 미사용
// =============================
/* USER CODE END 0 */
```
#### 3. 기타
- 방향 값을 `typedef enum { LOCKER_FORWARD, LOCKER_BACKWARD }`로 정의<br>
-> 의미를 명확히 하고, 값 사용 실수를 방지하며 향후 확장에도 유리함.
- `MPU6050_Init()` 실패 시 `Error_Handler()`를 호출하도록 수정<br>
-> 오류 발생 시 명확한 처리가 가능해졌고, 기존 코드처럼 무한 루프에 빠지는 문제를 방지함.
- 사용하지 않는 변수나 OLED 디버깅 코드 등을 정리/제거함으로써 코드의 불필요한 노이즈를 줄이고 가독성을 높임

### 수신부(Rx)
#### 1. Encoder 기반 RPM 측정 로직 추가
- 목적: DC 모터의 회전 속도를 실시간으로 측정하여 디버깅 및 제어 정확도 향상.
- 핵심 구현
    - TIM4 Encoder 모드를 이용하여 카운터 변화량 추적.
    - `Update_Motor_RPM()` 함수 내에서 100ms 주기로 엔코더 카운터 차이를 기반으로 RPM 계산.
    - `fabsf(((float)delta / TICKS_PER_REV) * 10 * 60)` 공식 사용.
    - OLED에 실시간 RPM 표시: `OLED_Display_Status()` 함수에서 `"RPM: %.1f"` 형태로 시각화. (향후 Car_status에서 구현)

#### 2. 핸들 스위치 토글 기반 전/후진 변속 로직 추가
- 목적: 핸들 스위치의 상태(RF 송신 데이터 포함)를 통해 실시간 전/후진 방향 제어.
- 핵심 구현
    - RF 패킷 내 `Byte 7`에 `direction` 값을 포함시켜 수신.
    - `typedef enum { DIRECTION_BACKWARD, DIRECTION_FORWARD } MotorDirection` 열거형 도입.
    - `motor_direction` 전역 변수로 방향 상태 유지.
    - `Update_Motor_Direction()` 함수에서 이전 방향과 비교해 GPIO IN1/IN2 제어 핀 변경.
    - 매크로 `MOTOR_FORWARD()`, `MOTOR_BACKWARD()`로 코드 가독성 및 재사용성 향상.

#### 3. 전체 코드 구조 및 유지보수성 개선
- main()에 혼재돼 있던 로직을 Control_, Update_, Parse_, OLED_ 등의 함수로 분리하여 가독성과 유지보수성 향상
- #define과 enum, 매크로를 활용 <br>(모터 방향 제어는 MOTOR_FORWARD(), MOTOR_BACKWARD() 매크로와 MotorDirection enum을 사용해 일관되게 처리)
- 구조적 리팩토링을 통해 가독성, 유지보수성, 확장성 강화

---

## 향후 확장 및 개선 아이디어
- 장애물을 초음파 센서로 감지 -> RF 통신을 통해 핸들로 전송, 핸들의 햅틱 센서로 운전자에게 진동 경고를 제공 
- (파이프라인 추가해 Rx와 Tx 역할을 교체하여 양방향 통신을 구현)

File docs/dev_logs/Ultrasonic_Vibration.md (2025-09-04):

# 초음파센서 거리값 기반 진동모터 햅틱 발생 로직 구현	

## 프로젝트 활용 방안
초음파 센서로 감지한 거리값을 기반으로, 일정 거리 이내 접근 시 진동모터를 작동시켜 운전자에게 직관적인 햅틱 경고를 제공함으로써 RC카의 충돌 방지 및 사용자 반응성을 향상시킴

---

## 이론 개요

### 트랜지스터 내장형 진동 모터 모듈
이 모듈은 S8050 NPN 트랜지스터를 내장하고 있으며, MCU 제어 신호로 진동 모터를 스위칭 구동하는 역할을 한다.

#### 진동 모터 모듈에서 트랜지스터의 역할
1. 신호 증폭
MCU의 디지털 출력은 수 mA 수준으로, 직접 모터를 구동하기엔 부족하기 때문에 내장된 트랜지스터가 이를 증폭하여 모터에 필요한 전류(최대 60~90mA)를 공급한다.

2. 전류 스위치 (Low-side Switching)
MCU에서 IN 핀에 HIGH 신호가 들어오면, 트랜지스터 베이스가 활성화되어
모터의 GND 경로가 열리며 모터가 진동하게 된다.

> [Vibration Motor Module datasheet](../datasheets/Vibration_Motor_Module_datasheet.pdf)

---

## 하드웨어 연결

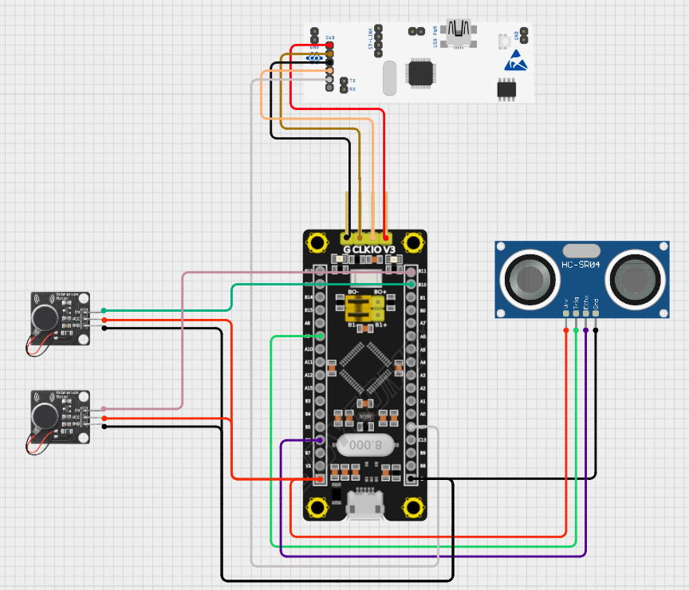
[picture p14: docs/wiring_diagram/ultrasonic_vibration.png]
초음파센서_진동모터 배선도


|F103보드|진동모터A,B|
|:---:|:---:|
|PB10|IN(모터A)|||
|PB11|IN(모터B)|||
|공통 GND|
|+5V|VCC(A,B)|

|F103보드|초음파센서|
|:---:|:---:|
|PA9|Trig|
|PB6|Echo|
|공통 GND|
|+5V|VCC|

---  

## STM32CubeMX 설정

### 진동모터

- PB10 : GPIO_Output
- PB11 : GPIO_Output

> [이전 초음파센서 ioc setting 참고](./Ultrasonic.md)
---
## 코드 설명
동작요약 : HAL_GetTick() 기반으로 100ms 주기로 초음파 센서를 트리거하고, 거리값(distance)이 10cm 이하일 때 진동 모터 2개를 동작시킴

```c
// 마지막으로 초음파 센서를 트리거한 시간(ms)을 저장하는 변수
uint32_t prev_tick = 0; 

while (1)
{
    // 현재 시간과 이전 시간 차이가 100ms 이상일 경우, 즉 0.1초 주기로 초음파 센서 트리거 및 모터 상태 갱신을 수행
    if (HAL_GetTick() - prev_tick >= 100)
    {
        prev_tick = HAL_GetTick();

        // 1) 초음파 센서의 Trig 핀에 10us 펄스를 줘서 거리 측정을 시작
        HAL_GPIO_WritePin(TRIG_PORT, TRIG_PIN, GPIO_PIN_SET);
        delay_us(10);
        HAL_GPIO_WritePin(TRIG_PORT, TRIG_PIN, GPIO_PIN_RESET);

        // 2) 거리값에 따른 진동 모터 제어
        if (distance <= 10 && distance > 0)
        {
            HAL_GPIO_WritePin(GPIOB, GPIO_PIN_10, GPIO_PIN_SET); // 모터A ON
            HAL_GPIO_WritePin(GPIOB, GPIO_PIN_11, GPIO_PIN_SET); // 모터B ON
        }
        else
        {
            HAL_GPIO_WritePin(GPIOB, GPIO_PIN_10, GPIO_PIN_RESET); // 모터A OFF
            HAL_GPIO_WritePin(GPIOB, GPIO_PIN_11, GPIO_PIN_RESET); // 모터B OFF
		}
	}
}
```

---

## 문제 해결 및 개선/확장

### 개선사항 
- HAL_Delay() 대신 HAL_GetTick() 기반으로 초음파 센서 측정 주기를 제어하도록 변경
- 기존 코드에서는 초음파 센서의 거리 측정을 위해 HAL_Delay(100) 함수를 사용하여 100ms의 고정 지연을 발생시켰음. 그러나 HAL_Delay()는 해당 시간 동안 CPU가 완전히 blocking되므로, 다른 작업을 동시에 수행할 수 없고, 향후 FreeRTOS와 같은 RTOS 환경 도입 시 충돌 위험이 존재함.

### 개선내용 
- HAL_GetTick() 함수는 시스템 시작 이후 경과된 시간을 ms 단위로 반환하는 비차단형 타이머 함수이며, 이를 이용해 측정 주기를 제어한다.

### 기대 효과
- 측정 주기의 정확도 향상 (밀리초 단위까지 정밀 제어)
- 메인 루프의 유연성 확보 (다른 기능과 병렬 처리 가능)
- RTOS 전환 시 유리한 구조 (Non-blocking 코드 → Task 기반 구조로 쉽게 포팅 가능)

---

## 향후 확장 및 개선 아이디어
- PWM 활용
    - 1. 충돌감지 거리 설정값 이하 근접 > 듀티비 50% 햅틱 발생<br>
    - 2. 충돌감지센서(향후 추가) 동작(차량이 물리적으로 충돌한 경우) > 듀티비 100% 햅틱 발생 (몇초간)
- RTC와 결합하여 충격 발생 시각 기록
    - SD카드나 외부 플래시에 저장 ("Crash @ 12:45:21, 강도: High" 등). 
- 구조를 RTOS task 기반으로 리팩토링

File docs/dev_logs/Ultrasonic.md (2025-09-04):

# [HC-SR04] 초음파센서 구현 로그

## 프로젝트 활용 방안
초음파 센서는 차량 전방의 장애물을 감지하기 위해 사용되며, 측정된 거리 데이터는 핸들에 연결된 진동모터 기반 충돌 방지 경고 시스템에 전달되어 운전자에게 피드백을 제공하는 데 활용된다.

---

## 이론 개요

### HC-SR04 동작원리
HC-SR04 초음파센서 모듈은 총 4개의 핀으로 구성되어 있으며, 각각 VCC, GND, Trig(트리거 핀), Echo(에코 핀)으로 구성된다. 초음파 센서는 자신과 앞에 놓인 물체 사이의 거리를 측정하며, 이는 40kHz 주파수의 초음파를 8회 발사함으로써 이루어진다. 방출된 신호가 송신된 직후 타이머가 시작되고, 초음파가 물체에 반사되어 수신기에 감지되면 타이머가 종료된다. 이때, 초음파가 왕복하는 데 걸린 시간을 측정하여 센서와 물체 사이의 거리를 계산할 수 있다.

HC-SR04 초음파 센서를 사용하기 위해서는 먼저 Trig 핀에 10마이크로초(μs)의 펄스 신호를 입력해야 하며, 이후 Echo 핀에서 출력되는 펄스의 폭(pulse width) 을 측정해야 한다.
이를 위해 Trig 핀에 연결된 GPIO를 출력 모드로 설정하고, 먼저 LOW 상태로 초기화한 후, 10μs 동안 HIGH 상태를 유지한 뒤 다시 LOW로 전환하여 트리거 펄스를 생성한다.
그 다음, Echo 핀에 연결된 GPIO를 입력 모드로 설정하고, 해당 핀이 HIGH 상태를 유지하는 시간을 측정함으로써 초음파가 반사되어 돌아오는 시간을 알 수 있다.
 
8회의 초음파 펄스는 공기 중에서 음속인 초속 340m의 속도로 이동하게 되며, 거리 = 속력 × 시간 공식을 통해 거리를 계산할 수 있다. 
단, 이 공식에서 사용되는 시간은 초음파가 물체까지 가는 시간뿐만 아니라 왕복 시간 (물체까지 가는 시간 + 다시 돌아오는 시간)을 포함하므로, 측정된 시간을 2로 나누어야 실제 거리를 얻을 수 있다.

공식 : Distance = (pulse_time × speed_of_sound) / 2 

> [HC-SR04 datasheet](../datasheets/HCSR04_datasheet.pdf)

---

## 하드웨어 연결

STM32F103에서 초음파 센서 HC-SR04의 Echo 핀은 5V 신호를 출력하므로, 이를 직접 GPIO에 연결할 경우 보드 손상의 위험이 있다. 
따라서 STM32F103의 데이터시트에서 해당 GPIO 핀이 FT(Five Volt Tolerant)로 명시되어 있는지를 반드시 확인해야 하며, <br>
FT로 표시된 핀은 5V 입력을 허용하므로 별도의 로직 레벨 시프터 없이도 안전하게 사용할 수 있다. <br>
반면 FT가 아닌 3.3V 전용 핀에 5V 신호를 입력하면 내부 회로가 손상될 수 있으므로 주의가 필요하다.

|초음파센서|F103보드|
|:---:|:---:|
|Vcc|5V|
|Gnd|Gnd|
|Trig|A9|
|Echo|A8|

---

## STM32CubeMX 설정
systemcore > sys > debug > Serial Wire
               > RCC > HSE > Crystal/Ceramic

clock configuration > HCLK를 72로, enter, ok

Timers > TIM1 > clock source : internal clock

parameter settings > prescaler : 71

PA9 -> gpio_output
PA8 -> gpio_input

save and generate code

참고한 링크에서 code copy, save and build로 오류 확인

debug > debugger > st-link (st-link gdb server) > reset behavior : sofware system reset > apply and ok

switch 누르고 live expressions 탭 > 코드의 distance 변수값 복사 > expressions에 붙여넣기 > start하면 거리값 출력됨

---
#### 폴링방식 기반 초음파센서 거리값 출력
## 코드 설명

본 프로젝트의 초음파센서 동작은 정확한 거리값이 필요한 것이 아니라 차량 충돌 방지를 위한 특정 범위의 거리값만 반환하면 되는 것이기 때문에 원활한 코드의 유지보수 목적으로  HAL 방식을 적용하였으며, 초기의 코드는 HC-SR04 초음파 센서의 동작을 GPIO polling 방식으로 구현한 것으로, STM32의 타이머(TIM1)를 이용해 펄스 폭을 직접 측정하여 거리(cm)를 계산하였다.

### 1. 핀 정의
```c
    #define TRIG_PIN GPIO_PIN_9
    #define ECHO_PIN GPIO_PIN_8
```
- TRIG_PIN은 초음파를 발사할 트리거 핀 (출력)
- ECHO_PIN은 반사된 초음파를 감지할 핀 (입력)

### 2. TRIG 펄스 생성
```c
HAL_GPIO_WritePin(TRIG_PORT, TRIG_PIN, GPIO_PIN_SET);
__HAL_TIM_SET_COUNTER(&htim1, 0);
while (__HAL_TIM_GET_COUNTER (&htim1) < 10);
HAL_GPIO_WritePin(TRIG_PORT, TRIG_PIN, GPIO_PIN_RESET);
```
- TRIG 핀을 10μs 동안 HIGH로 설정하여 초음파 발사 신호를 보냄

### 3. ECHO 핀의 펄스 폭 측정 (Polling 방식)
```c
while (!(HAL_GPIO_ReadPin (ECHO_PORT, ECHO_PIN)) && pMillis + 10 > HAL_GetTick());
Value1 = __HAL_TIM_GET_COUNTER (&htim1);

while ((HAL_GPIO_ReadPin (ECHO_PORT, ECHO_PIN)) && pMillis + 50 > HAL_GetTick());
Value2 = __HAL_TIM_GET_COUNTER (&htim1);
```
- 상승 에지(ECHO 핀이 HIGH 되는 시점): Value1에 저장
- 하강 에지(ECHO 핀이 LOW 되는 시점): Value2에 저장
- 타이머 값은 1 tick = 1μs 기준 → 펄스 폭 = Value2 - Value1

### 4. 거리 계산
```c
Distance = (Value2 - Value1) * 0.034 / 2;
```
- 초음파 왕복 시간에 음속(0.034 cm/μs) 을 곱한 뒤, 2로 나누어 편도 거리 계산

### 5. 오류 방지: Timeout 처리
```c
pMillis = HAL_GetTick();  // 현재 시간 기준
while (...) && pMillis + 10 > HAL_GetTick());
```
- ECHO 신호가 오지 않거나 너무 오래 걸리는 경우 무한 루프에 빠지지 않도록 timeout 구현

> 코드 참고 사이트 -> https://www.micropeta.com/video42<br>
> 참고링크 : https://www.youtube.com/watch?v=oD0mc6FXQ0s

---

## 문제 해결 및 개선/확장

#### 인터럽트 기반 타이머 인풋 캡쳐를 활용한 초음파센서 거리값 출력
### 1. 초기 코드 방식의 문제점
HC-SR04 초음파 센서의 Echo 신호의 상승과 하강을 while 루프 + 타이머로 직접 감지함

이 방식의 단점 : 
- while로 핀 상태를 폴링하기 때문에 CPU 점유율이 높음
- 디지털 신호의 미세한 변화(마이크로sec 단위)는 폴링 방식으로는 잡기 어려움
- 중간에 인터럽트가 들어오거나 오버헤드가 있으면 오차 발생

### 2. 코드 개선 방향
" Timer input capture 사용해서 업그레이드 "

Timer input capture를 사용하면
- 타이머가 외부 핀의 상승/하강 엣지를 자동으로 캡처함

- 캡처 순간의 정확한 타이머 카운터 값이 저장되어 μs 단위의 정확한 시간 측정 가능

- 인터럽트 기반이므로 CPU 점유율이 거의 없음

(STM32F103C8T6 기준, TIM2~TIM4에서 Input Capture 가능)<br><br>

### 3. 하드웨어 연결 및 CubeMX 설정

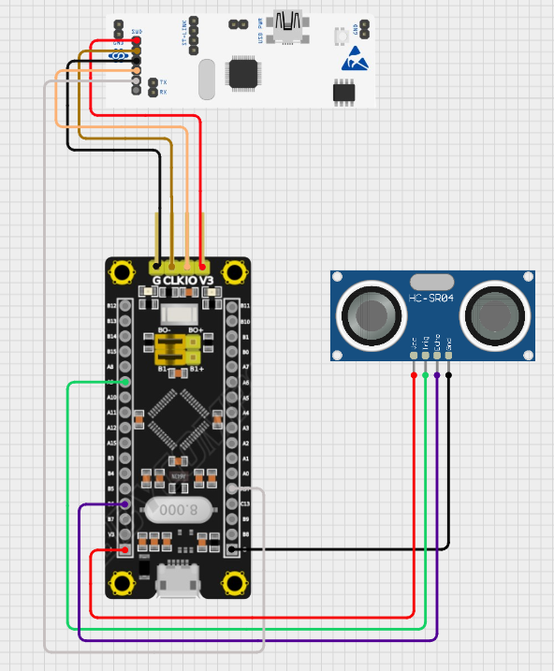
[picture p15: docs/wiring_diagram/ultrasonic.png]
초음파센서 결선도


Timer Input Capture가 가능한 핀을 Echo에 연결 (PB6 선택)

|초음파센서|F103보드|
|:---:|:---:|
|Vcc|5V|
|Gnd|Gnd|
|Trig|A9|
|Echo|PB6|

Timer를 Input Capture 모드로 설정 (상승 엣지/하강 엣지 감지 목적)

(tim4, ch1, echo를 pb6으로 사용)<br>
TIM4 → Channel1 → Input Capture 설정

PB6 → Alternate Function, Input Capture 모드

NVIC → TIM4 global interrupt enable

GPIOA9 → Output (TRIG)

### 4. 코드의 핵심 기능 요약

**Timer Input Capture 기반 거리 측정**

1. Trig 신호 발생 (출력)
TRIG_PIN (GPIOA PIN9)을 10μs 동안 HIGH로 설정하여 초음파 발사 신호를 보냄

```c
    HAL_GPIO_WritePin(TRIG_PORT, TRIG_PIN, GPIO_PIN_SET);
    delay_us(10);  // 10μs 유지
    HAL_GPIO_WritePin(TRIG_PORT, TRIG_PIN, GPIO_PIN_RESET);
```

2. Echo 신호 측정 (입력 캡처)
초음파가 반사되어 돌아오면, Echo 핀에서 HIGH 펄스가 발생. <br> TIM4의 CH1 (GPIOA PIN6 등)을 Input Capture 모드로 설정하여 펄스 폭을 측정함

```c
    htim4.Init.Prescaler = 71;     // 72MHz / (71+1) = 1MHz → 1 tick = 1μs
    htim4.Init.Period = 65535;     // 최대 65535μs 측정 가능
```

3. Input Capture 동작 흐름
```c
    HAL_TIM_IC_Start_IT(&htim4, TIM_CHANNEL_1);  // 인터럽트 기반 입력 캡처 시작
```
- 첫 번째 인터럽트 발생 시: 
    - 상승 에지(RISING) 감지 → ic_val1 저장
    - 다음 캡처를 위해 감지 방향을 하강 에지(FALLING)로 전환

- 두 번째 인터럽트 발생 시:
    - 하강 에지(FALLING) 감지 → ic_val2 저장
    - 펄스 폭 계산: ic_val2 - ic_val1 (단, 오버플로우 보정 포함)

- 거리 계산:
```c
    distance = (diff * 0.0343f) / 2.0f;
```
※ 여기서 0.0343f는 음속 343 m/s를 μs 단위로 변환한 값 (cm/μs)

---

## 향후 확장 및 개선 아이디어
- 거리 제한값 초과 시 이벤트 처리 추가
- FreeRTOS task로 나누는 방식
- 거리 값 평균 필터 적용

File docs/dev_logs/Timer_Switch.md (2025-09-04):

# [타이머 인터럽트 기반] 버튼 눌림 시간 측정 및 OLED 출력

## 프로젝트 개요

본 프로젝트는 STM32F103C8T6 보드에서 **외부 인터럽트와 타이머 인터럽트**를 이용하여 두 개의 버튼 입력 시간(가속/브레이크)을 측정하고, 이를 **I2C 기반 OLED(SSD1306)** 화면에 실시간으로 출력하는 시스템을 구현한다.  
이를 통해 사용자의 입력 지속 시간(Press Duration)을 시각적으로 모니터링할 수 있으며, 차량 제어 입력 분석, 디버깅, UI 피드백 등에 활용할 수 있다.

---

## 이론 개요

### 버튼 입력 시간 측정 원리

1. **외부 인터럽트 (EXTI)**
   - 버튼 핀(PB0: Accel, PB1: Brake)에 입력 변화가 감지되면 인터럽트 발생
   - **GPIO_PIN_RESET → 눌림**, **GPIO_PIN_SET → 떼짐**
   - 눌림이 감지되면 `pressed` 플래그를 `1`로 설정하고, 카운트 초기화
   - 떼짐이 감지되면 `pressed` 플래그를 `0`으로 설정

2. **타이머 인터럽트 (TIM2)**
   - 20ms 주기로 반복 발생
   - 버튼이 눌려 있는 동안 카운트를 증가시킴 (`count++`)
   - 누적된 카운트를 `count * 20`으로 변환하여 **ms 단위 시간** 계산

3. **OLED 출력**
   - OLED에 버튼 이름과 함께 누적 시간(예: ACC: 240ms) 출력

---

## 하드웨어 연결

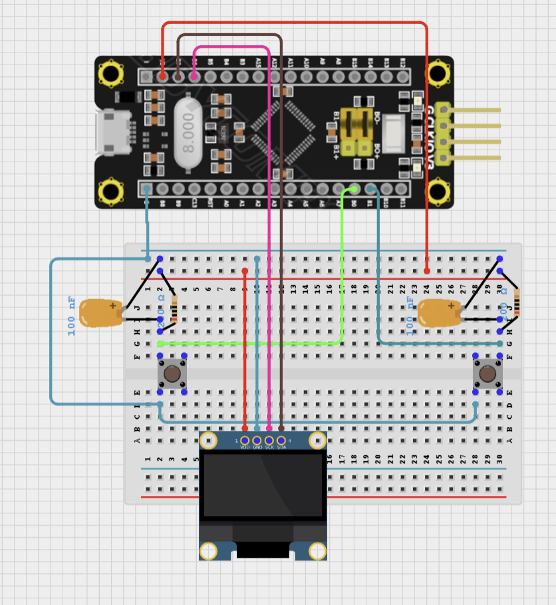
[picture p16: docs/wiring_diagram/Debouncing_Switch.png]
스위치 회로


| 기능 | STM32 핀 | 연결 대상 |
|---|---|---|
| Accel 버튼 | PB0 | 택트 스위치  |
| Brake 버튼 | PB1 | 택트 스위치  |
| OLED SDA | PB7 (I2C1_SDA) | SSD1306 |
| OLED SCL | PB6 (I2C1_SCL) | SSD1306 |

> 버튼은 외부 풀업 저항에 연결되어 있으며,  
눌렀을 때 `LOW`(0V) 상태가 되도록 연결  
0.1μF 커패시터 장착 (HW 디바운싱 처리)
---

## STM32CubeMX 설정 요약

### GPIO
- PB0, PB1: EXTI Interrupt (Rising and Falling edge)
- 내부 풀업 저항 비활성화

### I2C
- I2C1: SSD1306 연결 (400kHz)

### TIM2
- Prescaler: 71
- Period: 19999

---

## 주요 코드 설명

### 외부 인터럽트 핸들러 (HAL_GPIO_EXTI_Callback)

```c
void HAL_GPIO_EXTI_Callback(uint16_t GPIO_Pin)
{
    uint32_t now = HAL_GetTick();

    if (GPIO_Pin == GPIO_PIN_0)  // Accel 버튼
    {
        if (HAL_GPIO_ReadPin(GPIOB, GPIO_PIN_0) == GPIO_PIN_RESET) {
            accel_pressed = 1;
            accel_count = 0;
            prev_tick_accel = now;
        } else {
            accel_pressed = 0;
            prev_tick_accel = now;
        }
    }
    else if (GPIO_Pin == GPIO_PIN_1)  // Brake 버튼
    {
        if (HAL_GPIO_ReadPin(GPIOB, GPIO_PIN_1) == GPIO_PIN_RESET) {
            brake_pressed = 1;
            brake_count = 0;
            prev_tick_brake = now;
        } else {
            brake_pressed = 0;
            prev_tick_brake = now;
        }
    }
}
```

### 타이머 인터럽트 핸들러 (HAL_TIM_PeriodElapsedCallback)

```c
void HAL_TIM_PeriodElapsedCallback(TIM_HandleTypeDef *htim)
{
    if (htim->Instance == TIM2)
    {
        if (accel_pressed) accel_count++;
        if (brake_pressed) brake_count++;

        char buffer1[20], buffer2[20];

        snprintf(buffer1, sizeof(buffer1), "ACC: %lums", accel_count * 20);
        SSD1306_GotoXY(0, 0);
        SSD1306_Puts(buffer1, &Font_11x18, 1);

        snprintf(buffer2, sizeof(buffer2), "BRK: %lums", brake_count * 20);
        SSD1306_GotoXY(0, 20);
        SSD1306_Puts(buffer2, &Font_11x18, 1);

        SSD1306_UpdateScreen();
    }
}
```
# 코드 스크립트용
```
  /* USER CODE BEGIN 2 */
  SSD1306_Init();
    HAL_TIM_Base_Start_IT(&htim2);
  /* USER CODE END 2 */

/* USER CODE BEGIN 4 */
void HAL_GPIO_EXTI_Callback(uint16_t GPIO_Pin)
{
    uint32_t now = HAL_GetTick();

    if (GPIO_Pin == GPIO_PIN_0)  // Accel 버튼
    {
        if (HAL_GPIO_ReadPin(GPIOB, GPIO_PIN_0) == GPIO_PIN_RESET)
        {
            // 눌림이 감지된 순간(하강), 디바운싱 여부와 상관없이 초기화
            accel_pressed = 1;
            accel_count = 0;
            prev_tick_accel = now;
        }
        else
        {
            // 떼짐(상승)은 즉시 pressed=0 처리
            accel_pressed = 0;
            prev_tick_accel = now;
        }
    }
    else if (GPIO_Pin == GPIO_PIN_1)  // Brake 버튼
    {
        if (HAL_GPIO_ReadPin(GPIOB, GPIO_PIN_1) == GPIO_PIN_RESET)
        {
            // 눌림이 감지된 순간(하강), 디바운싱 여부와 상관없이 초기화
            brake_pressed = 1;
            brake_count = 0;
            prev_tick_brake = now;
        }
        else
        {
            // 떼짐(상승)은 즉시 pressed=0 처리
            brake_pressed = 0;
            prev_tick_brake = now;
        }
    }
}

void HAL_TIM_PeriodElapsedCallback(TIM_HandleTypeDef *htim)
{
    if (htim->Instance == TIM2) // 20ms 주기 타이머
    {
        if (accel_pressed) accel_count++;
        if (brake_pressed) brake_count++;

        char buffer1[20], buffer2[20];

        snprintf(buffer1, sizeof(buffer1), "ACC: %lums", accel_count * 20);
        SSD1306_GotoXY(0, 0);
        SSD1306_Puts(buffer1, &Font_11x18, 1);

        snprintf(buffer2, sizeof(buffer2), "BRK: %lums", brake_count * 20);
        SSD1306_GotoXY(0, 20);
        SSD1306_Puts(buffer2, &Font_11x18, 1);

        SSD1306_UpdateScreen();
    }
/* USER CODE END 4 */
```

---

## 요약 흐름도

1. **버튼 누름** → EXTI 인터럽트 발생 → `pressed = 1`, `count = 0`
2. **버튼 유지** → TIM2 인터럽트 20ms마다 `count++`
3. **버튼 뗌** → EXTI 인터럽트로 `pressed = 0` 설정
4. OLED에 측정된 시간(`count * 20ms`) 표시

---

## 확장 아이디어
- 버튼 누름 시간에 따라 모터 제어
- OLED 그래픽 막대(Progress Bar)로 시각화
- FreeRTOS 적용 시 Task로 측정 로직 분리
- 무선 통신 모듈 연동 시 누름 시간 전송

---

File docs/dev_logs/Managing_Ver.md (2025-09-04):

# Embedded Git Versioning Guide with CubeIDE

STM32 기반 임베디드 프로젝트를 GitHub와 CubeIDE를 연동하여 버전 관리할 때 고려해야 할 구조와 정책 정리

---

## 왜 GitHub에서 프로젝트 단위로 버전 관리를 하는가?

- **MCU별로 프로젝트가 명확히 분리되기 때문**  
  STM32 프로젝트는 MCU 종류 및 핀 설정에 따라 디렉토리 구조와 코드가 독립적으로 구성됨  
  → *기능별 서브 디렉토리보다, 프로젝트 자체가 하나의 독립 단위로 취급되어야 함*

- **파일 시스템 스냅샷이 아닌 시분할 변경 이력 관리가 가능**  
  Git은 특정 시점에서의 파일 상태를 단순히 저장하는 것이 아니라,  
  *변경의 흐름(history)을 시간 축 상에서 관리하는 시분할 기반 관리 체계*

- **원격 저장소(GitHub)가 메인 저장소이며, 로컬은 캐시 혹은 복사본**  
  원격 저장소를 기준으로 버전 정합성을 유지해야 하며,  
  CubeIDE에서의 작업은 반드시 커밋 후 푸시(push)하여 GitHub에 반영

---

## 태그(Tag)와 커밋(Commit)의 사용 전략

### 태그는 언제 붙이는가?

- **모듈 단위 테스트 후 → 태그 없이 커밋만 수행**
- **여러 모듈을 통합하여 안정화가 완료된 시점 → 태그 부여**
- **예외 상황: RTOS 통합, 시스템 구조 변경 등 큰 변경이 있을 때도 태그 적용**

### 태그 네이밍 규칙

- **시맨틱 버전 형식 사용: `vMajor.Minor.Patch`**
  - `v1.0.0` → 첫 번째 전체 통합 및 안정화 버전
  - `v1.1.0` → 주요 로직 추가 (ex. 외부 인터럽트 기능 추가)
  - `v2.0.0` → 구조적으로 큰 변화 (ex. FreeRTOS 도입 및 병합)

### 예시 흐름

| 작업 단계 | Git 사용 방식 | 비고 |
|---|---|---|
| 모듈별 단위 개발 | 커밋만 사용 | 기능 확인 시점마다 저장 |
| ioc 통합 완료 | 태그: `v1.0.0` 부여 | 코드 안정화, 전체 빌드 가능 |
| RTOS 도입 | 태그: `v2.0.0` 부여 | 구조 변경, 병합 완료 |
| 이후 기능 개선 | 커밋 또는 `v2.1.0`, `v2.1.1` | 변경 규모에 따라 결정 |

---

## CubeIDE에서 태그 등록/삭제 후 push 방법
1. CubeIDE에서 변경 사항을 커밋 및 Push
2. Git Bash에서 다음 명령 실행

### 태그 생성
ex) sensor

```bash
// 1. 원하는 브랜치로 이동
git checkout Unit_car_status 

// 2. 로컬에 태그 생성
// 2-1. 가장 최근 커밋(HEAD)에 태그 (기본값)
git tag -a sensor_v1.5.0 -m "car_status 통합 완료"
// 2-2. 원하는 커밋 해시를 지정해서 태그 (7자리)
git tag -a sensor_v1.5.0 <커밋해시7자리> -m "car_status 통합 완료"

// 3. 원격으로 push 반영
git push origin sensor_v1.5.0
```
- `-a` : annotated tag (메세지 포함, 사용자 이름/날짜 저장됨)
- `-m` : 메세지 작성
- 해당 태그는 sensor_v1.5.0이라는 버전으로 GitHub 저장소에 명확히 표시되며,
이후 버그 수정 또는 확장 개발 시 기준점으로 활용 가능함

### 태그제거
ex) sensor
```bash
// 1. 원하는 브랜치 이동
git checkout Unit_car_sensor

// 2. 로컬의 태그 제거 (달았던 태그명 그대로)
git tag -d sensor_v1.0.0

// 3. 원격으로 push 반영
git push origin :refs/tags/sensor_v1.0.0
```

---

## Git vs 파일 시스템의 버전 관리 차이

| 항목 | Git 버전 관리 | 일반 파일 백업 |
|---|---|---|
| 저장 방식 | 변경 이력 기반, 시분할 스냅샷 | 단순 복사본 |
| 협업 | 브랜치 및 태그 기반 분기 협업 | 수동 파일 공유 |
| 태그/커밋 이력 관리 | 정밀 추적 및 복구 가능 | 시점 구분 어려움 |
| CubeIDE 연동 | `.git`과 `.project` 연계하여 구조 유지 | IDE 자체 백업 기능과는 별개 |

---

## 프로젝트 구조

```
Unit_controller/
├── Inc/
├── Src/
├── feature/
│   ├── button/
│   ├── gyro/
│   ├── dc_motor/
│   └── lcd_display/
├── main.c
└── README.md
```
> 한 브렌치 당 한 프로젝트 파일로 관리, 커밋으로 이력 추적  
> 하나의 유닛 (mcu) 에 개발 흐름을 분기할 수 있는 효율적인 구조

---
## 모듈 테스트 히스토리

| 커밋해시값 | 날짜 | 변경 내용 |
|---|---|---|
| [`82d4624`](https://github.com/YeonsuJ/Car_control_project/commit/82d462479a9bef4ad92decd2cc37d7a1186b770f) | 2025-05-19 | - 버튼 입력 처리<br>- DC 모터 정/역 제어 |
| [`2cbdb42`](https://github.com/YeonsuJ/Car_control_project/commit/2cbdb42c721dd69e062f97b6757ff0f06227f0a2) | 2025-06-02 | - 자이로 센서 기능 추가<br>- 자이로 기반 방향 제어 |

---
## 버전 히스토리

| 버전 | 날짜 | 변경 내용 |
|---|---|---|
| v1.0.0 | 2025-05-19 | - 버튼 입력 처리<br>- DC 모터 정/역 제어 |
| v1.1.0 | 2025-06-02 | - 자이로 센서 기능 추가<br>- 자이로 기반 방향 제어 |
| v1.2.0 | 2025-06-10 | - OLED 출력 기능 추가<br>- 상태 정보 출력 |
| v2.0.0 | 예정 | - RTOS 도입 및 구조 개편<br>- 모듈 분리 및 스케줄링 기능 추가 예정 |

> 태그는 통합 완료된 버전만 명시적으로 관리하며, 중간 모듈 개발은 커밋 기반으로 추적

---

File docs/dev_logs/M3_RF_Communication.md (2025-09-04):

# RF 기반 자이로 핸들 입력 및 버튼 상태 송수신 시스템

## 프로젝트 활용 방안
본 프로젝트는 무선 핸들을 통해 RC카를 제어하는 시스템의 핵심 데이터인 **자이로센서 기반 roll 값**과 **악셀(acc), 브레이크(brk) 버튼의 눌림 시간**을 **NRF24L01+ RF 모듈**을 통해 송수신함으로써, RC카의 조향 및 가감속 제어를 가능하게 한다. 송신부와 수신부 모두 STM32F103C8T6 MCU 기반이며, 송신부는 사용자 입력과 센서 데이터를 취합해 RF 패킷을 전송하고 수신부는 이 패킷을 해석하여 모터를 직접 구동하는 방식으로 실시간 양방향 제어 시스템을 구현하도록 한다.

---

## 이론 개요

### 관련 기술 개요

**NRF24L01+ 모듈**은 2.4GHz 주파수 대역에서 동작하는 **무선 송수신기**로, SPI(Serial Peripheral Interface)를 통해 MCU와 연결된다. 이 모듈은 **최대 10Mbps의 SPI 통신 속도**와 **1Mbps~2Mbps의 무선 전송률**을 지원하며, 저전력 고성능 무선 통신이 필요한 IoT, RC카, 센서 네트워크 등에 널리 사용된다.

### 핵심 동작 원리

1. **SPI 통신 흐름**  
   - MCU(Master)가 SCK(클럭), MOSI(데이터 출력), MISO(데이터 입력), CSN(슬레이브 선택) 핀을 통해 **NRF24L01+ 모듈(Slave)**과 **Full-duplex 방식**으로 통신한다.
   - CSN 핀이 LOW가 되면 전송 개시, HIGH가 되면 종료된다.
   - 송신 시 CE 핀을 HIGH로 설정해 데이터를 무선으로 전송하고, 수신 시에는 CE를 계속 HIGH로 유지해 대기 모드로 둔다.

2. **NRF24 RF 통신 절차**  
   - 송신부는 미리 설정된 파이프 주소와 채널을 기반으로 데이터를 전송한다.
   - 수신부는 동일한 파이프 주소와 채널을 수신 대기 상태로 설정하여 일치하는 데이터만을 수신한다.
   - 데이터 수신 시, IRQ 핀을 통해 인터럽트 신호를 발생시켜 MCU가 이를 감지할 수 있게 한다.
   - Auto ACK 기능이 활성화되어 있으면 수신 성공 시 자동으로 송신부에 응답 신호가 전송된다.

- 이 프로젝트는 **MIT 라이선스를 따르는 [stm32_hal_nrf24_library](https://github.com/developer328/stm32_hal_nrf24_library)**를 사용하였으며, 다음 4개의 주요 파일로 구성된다:
  - `NRF24.c`
  - `NRF24.h`
  - `NRF24_conf.h`
  - `NRF24_reg_addresses.h`

---

## 하드웨어 연결

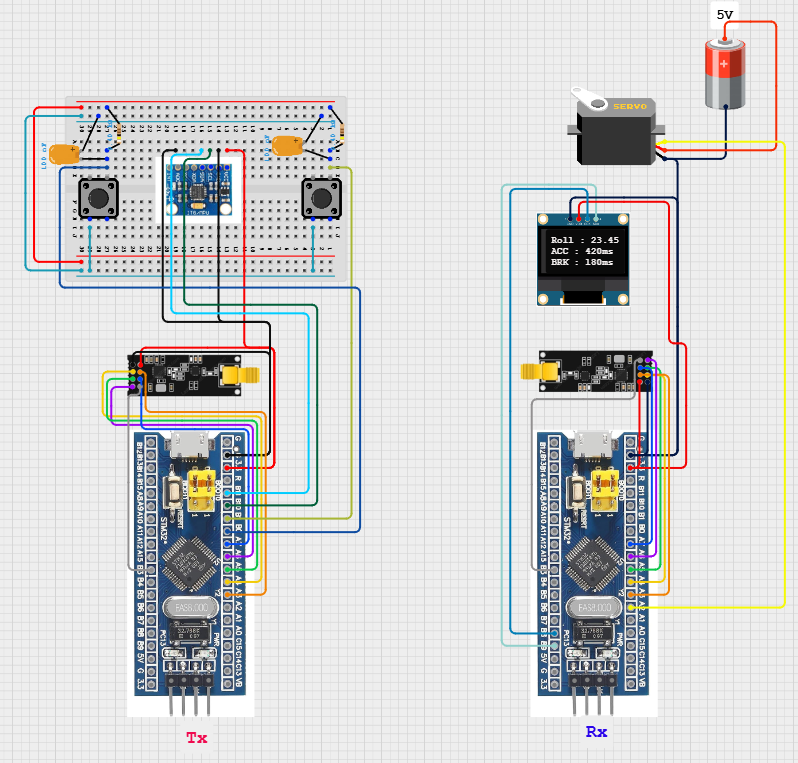
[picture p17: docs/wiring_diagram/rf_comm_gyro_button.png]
RF통신 배선도


---

## STM32CubeMX 설정

### 기본 설정 요약

#### SPI1 설정
- **Mode**: Full-Duplex Master  
- **Prescaler**: 16 → 실제 Baud Rate: **4.5 Mbps**  
NRF24L01+의 허용 SPI 속도는 최대 10Mbps

#### GPIO 핀 설정

| 기능 | 핀 번호 | 모드 | 설명 |
|---|---|---|---|
| MISO | PA6 | Alternate Function | SPI 수신 |
| MOSI | PA7 | Alternate Function | SPI 송신 |
| SCK | PA5 | Alternate Function | SPI 클럭 |
| CSN | PA3 | Output Push-Pull | Maximum output speed → HIGH |
| CE | PA4 | Output Push-Pull | Maximum output speed → HIGH |
| IRQ | PB3 | External Interrupt | EXTI3, Falling Edge 인터럽트 |

- **CSN/CE 핀은 NRF24 제어 신호로 사용되며**, 통신 안정성을 위해 `Output mode`와 함께 **최대 출력 속도(High speed)**로 설정해야 한다. 왜냐하면 낮은 속도에서는 SPI 클럭 타이밍에 비해 반응이 지연되어 통신 오류가 발생할 수 있기 때문이다.
- **IRQ 핀은 Falling Edge로 설정**해야 NRF24L01+ 모듈이 내부 수신 버퍼에 데이터가 도착했을 때 **하강 에지 신호로 인터럽트를 발생**시킬 수 있다. Rising 또는 Level Trigger 방식은 NRF24의 하드웨어 동작 방식과 맞지 않아 인터럽트가 발생하지 않을 수 있다.

---

## 전체 시스템 동작 흐름 요약

1. **송신부(STM32F103C8T6)**  
   - 자이로센서 MPU6050에서 roll 값을 읽고, 버튼 인터럽트를 통해 acc, brk 눌림 시간을 20ms 주기로 누적 측정  
   - int16_t, uint16_t, uint16_t 형식으로 패킹 후 20ms 간격으로 `nrf24_transmit()` 함수로 전송

2. **수신부(STM32F103C8T6)**  
   - EXTI3(PB3) 인터럽트를 통해 수신 이벤트 감지  
   - roll 값으로 서보모터 실시간 PWM 제어, 동시에 acc/brk, roll 값은 OLED에 디스플레이

> 실시간 무선 통신의 효율성과 MCU 연산 오버헤드를 고려하여, 부동소수점(float) 데이터를 직접 송신하는 방식은 배제하였다.  
> float을 무선 전송하려면 IEEE-754 형식으로 직렬화하고, 수신 후 다시 역직렬화(Deserialization)해야 하며, 이는 알고리즘 복잡도 및 코드 크기를 증가시키고 통신 오류 가능성도 높인다.  
> 따라서 본 프로젝트에서는 `float`형 roll 값을 송신 전 `int16_t` 타입으로 100배 스케일링하여 정수로 변환한 뒤 전송하고, 수신 시 다시 나누어 복원하는 구조를 채택하였다.
---
## 송신부 동작 요약

### 초기화 절차

```c
  SSD1306_Init();
  while (MPU6050_Init(&hi2c2) == 1);
  HAL_TIM_Base_Start_IT(&htim2);

  csn_high();
  ce_high();
  HAL_Delay(5);
  ce_low();

  nrf24_init();
  nrf24_stop_listen();  // 송신기이므로 listen 비활성화

  nrf24_auto_ack_all(auto_ack);
  nrf24_en_ack_pld(disable);
  nrf24_dpl(disable);
  nrf24_set_crc(no_crc, _1byte);

  nrf24_tx_pwr(_0dbm);
  nrf24_data_rate(_1mbps);
  nrf24_set_channel(90);
  nrf24_set_addr_width(5);
  nrf24_set_rx_dpl(0, disable);
  nrf24_pipe_pld_size(0, PLD_S);
  nrf24_auto_retr_delay(4);
  nrf24_auto_retr_limit(10);

  nrf24_open_tx_pipe(tx_addr);
  ce_high();
```

- **roll 값 측정 및 변환**:  
  MPU6050 센서에서 읽어온 roll 각도 값(float)을 100배 스케일링하여 `int16_t`로 변환한 뒤 전송한다.  
  이 방식은 `float`의 무선 전송 부담을 줄이기 위한 정수화 처리이며, 수신부에서는 다시 `float`으로 복원한다.

```c
MPU6050_Read_All(&hi2c2, &MPU6050);
float roll = MPU6050.KalmanAngleX;
int16_t roll_encoded = (int16_t)(roll * 100.0f);
```

- **acc/brk 값**: 버튼이 눌린 시간(ms)을 20ms 단위로 측정하여 `uint16_t`로 전송
- **전송 주기**: `HAL_GetTick()` 기준 20ms 주기 송신
- **전송 데이터 구조** (`uint8_t dataT[32]`):
  - `dataT[0]`: 식별자 (`0x01`)
  - `dataT[1~2]`: roll (int16_t)
  - `dataT[3~4]`: acc 시간 (uint16_t)
  - `dataT[5~6]`: brk 시간 (uint16_t)

```c
dataT[0] = 1;
memcpy(&dataT[1], &roll_encoded, sizeof(int16_t));
memcpy(&dataT[3], &accel_ms, sizeof(uint16_t));
memcpy(&dataT[5], &brake_ms, sizeof(uint16_t));
nrf24_transmit(dataT, 32); 
```

> 이 구조는 송신부에서의 데이터 용량 최소화와 실시간 전송의 안정성을 동시에 만족시키며, 수신부에서는 `roll = (float)roll_encoded / 100.0f` 방식으로 원래 각도를 복원한다.

---
## 수신부 동작 요약

### 초기화 절차

```c
SSD1306_Init();
HAL_TIM_PWM_Start(&htim2, TIM_CHANNEL_3);
HAL_TIM_Base_Start_IT(&htim2);

nrf24_init();
nrf24_stop_listen();
nrf24_auto_ack_all(auto_ack);
nrf24_en_ack_pld(disable);
nrf24_dpl(disable);
nrf24_set_crc(no_crc, _1byte);
nrf24_tx_pwr(_0dbm);
nrf24_data_rate(_1mbps);
nrf24_set_channel(90);
nrf24_set_addr_width(5);
nrf24_pipe_pld_size(0, 32);
nrf24_open_rx_pipe(0, rx_addr);
nrf24_listen();
```

### 수신 로직

- EXTI3(PB3) 인터럽트 → `nrf24_data_available()` → `nrf24_receive()` 호출
- 데이터 해석 구조:
  - `rx_buffer[0]`: 식별자
  - `rx_buffer[1~2]`: roll (int16_t)
  - `rx_buffer[3~4]`: accel_ms (uint16_t)
  - `rx_buffer[5~6]`: brake_ms (uint16_t)

```c
if (rx_buffer[0] == 1) {
    memcpy(&roll_encoded, &rx_buffer[1], sizeof(int16_t));
    received_roll = ((float)roll_encoded) / 100.0f;

    memcpy(&received_accel_ms, &rx_buffer[3], sizeof(uint16_t));
    memcpy(&received_brake_ms, &rx_buffer[5], sizeof(uint16_t));

    new_data_flag = 1;
}
```

- OLED 출력 예시:

```
Roll: 23.45
ACC:  420ms
BRK:  180ms
```

- PWM 서보 제어:

```c
float angle = received_roll + 90.0f;
uint16_t pwm = 500 + (angle / 180.0f) * 2000.0f;
__HAL_TIM_SET_COMPARE(&htim2, TIM_CHANNEL_3, pwm);
```

> `roll > 0` → 좌회전  
> `roll < 0` → 우회전

---

## 문제 해결 및 개선/확장

### 개선 포인트

- `HAL_Delay()` 제거, `HAL_GetTick()` 기반 주기 처리 → non-blocking 구조
- 인터럽트 기반 수신 처리 → 실시간 반응성과 CPU 효율 개선

### 향후 개선 아이디어 
- RTC 및 외부 저장장치(SD 카드 등) 연동하여 조향 및 이벤트 로그 기록  
- RTOS Task 구조로 확장 가능

---

## 참고 링크

- [stm32_hal_nrf24_library (MIT License)](https://github.com/developer328/stm32_hal_nrf24_library)

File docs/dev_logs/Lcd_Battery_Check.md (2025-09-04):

# [I2C 16x2 LCD] 배터리 잔량 측정 LCD 모니터링 로직 구현

## 프로젝트 활용 방안
LCD 디스플레이는 차량 후방에 장착되어, 주행 전 차량의 배터리 잔량, 각 MCU 간의 통신 상태, 차량과 핸들 간의 통신 상태 등을 확인하는 용도로 사용된다. 해당 정보는 실시간 출력이 요구되지 않기 때문에, 다중 슬레이브 연결이 가능하고 하드웨어 자원 소모가 적은 I2C 방식의 LCD 디스플레이를 채택하였다.

---

## 이론 개요

### LCD display 동작원리

이 디스플레이 모듈은 HD44780 문자 LCD와 PCF8574T I/O 확장 칩이 결합된 구조로, MCU에서 I2C를 통해 전송한 데이터를 PCF8574T가 8비트 병렬 신호로 변환하여 HD44780에 전달하고, 이를 통해 문자가 LCD에 출력되는 방식으로 동작한다. 5V의 전압에서 동작 하며, SDA, SCL 두 핀만으로 제어가 가능해 I/O 핀을 절약할 수 있다.

### ADC(아날로그-디지털 변환)로 배터리 잔량 측정 원리
STM32F103 보드의 ADC는 입력된 아날로그 전압을 기준 전압(Vref, 일반적으로 3.3V)을 기준으로 12비트 해상도(0~4095의 정수)로 디지털 값으로 변환하는 장치로, 예를 들어 1.65V 입력 시 2047 정도의 값을 출력한다. 본 프로젝트에서 사용하는 3.7V 리튬이온 배터리는 방전 상태에 따라 전압이 달라지므로, 이 전압을 측정하여 계산하면 대략적인 잔량(%)을 추정할 수 있다.

> [LCD display datasheet](../datasheets/I2C_1602_LCD.pdf)<br>
> [STM32F103C8T6 datasheet](../datasheets/STM32F103C8T6_datasheet.pdf)
---

## 하드웨어 연결

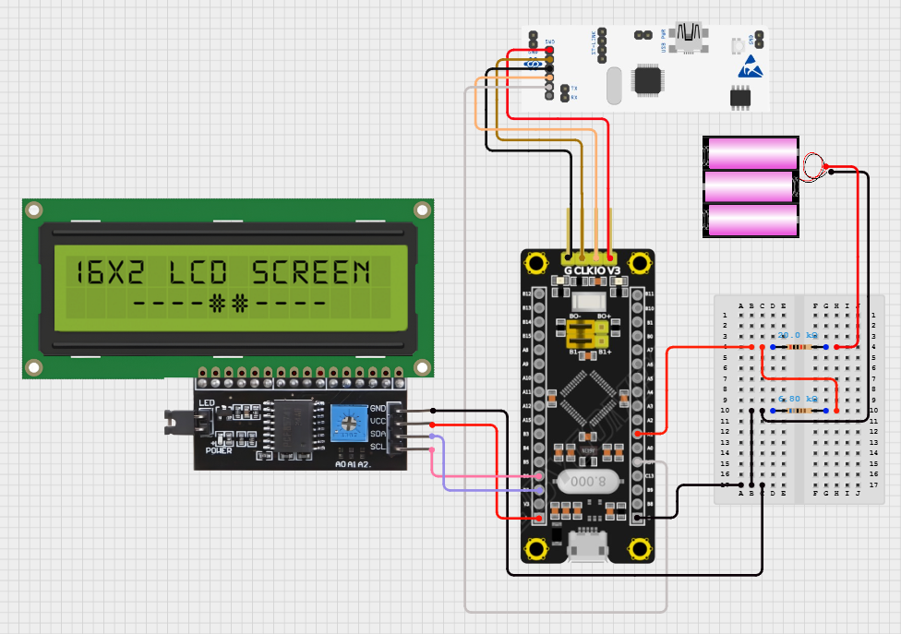
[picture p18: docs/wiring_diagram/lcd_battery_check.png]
LCD 디스플레이 배터리 잔량 결선도


### LCD 디스플레이

datasheet를 통해 FT(five volt tolerant 핀 확인해야함)

|LCD display|F103보드|
|:---:|:---:|
|Vcc|5V|
|Gnd|Gnd|
|SDA|B7|
|SCL|B6|

### ADC 분압회로 연결
STM32의 ADC 핀은 3.3V를 초과하는 전압을 허용하지 않기 때문에, 최대 12.6V(3.7v 직렬 3구)까지 도달하는 배터리 전압을 안전하게 측정하기 위해 저항 분압 회로를 구성하여 이를 약 3.2V 수준으로 낮춘 후 ADC에 입력한다.

### 원하는 분압 비율: R2/(R1+R2) = 3.2/12.6 = 0.254

### R1, R2 계산식

R2/(R1+R2)= 0.254= 1/(R1/R2)+1 = 약0.254
R1/R2 = 1/0.254-1 = 약 2.94
즉, R1은 2.94xR2와 근접함

표준저항에서 선택하면, R1=20k, R2=6.8k로 선택할 수 있음

```yaml
(+) 배터리 (3.7v 3S = 12.6V)
   |
   |
  [ R1 = 20kΩ ]
   |
   |---------> Vout 3.2V (F103보드 PA1)
   |
  [ R2 = 6.8kΩ ]
   |
   |
  GND (공통)
```
---

## STM32CubeMX 설정

### LCD 디스플레이
system core > sys > debug: serial wire

connectivity > i2c1 > i2c로 설정

<라이브러리 추가>
Core/Inc/liquidcrystal_i2c.h
Core/Src/liquidcrystal_i2c.h 

<liquidcrystal_i2c.h의 device i2c address 수정>
datasheet을 통해 i2c 주소를 0x27로 설정하면 되는 것을 확인<br>
#define DEVICE_ADDR     (0x3F << 1) 을 (0x27 << 1)로 바꾸기<br>
#include "stm32f1xx_hal.h" 로 수정

※ **I2C 장치중에서 Address를 확실하게 모를때**<br>
아래 코드를 넣고 출력을 하면 간단하게 7비트 Address를 확인할 수 있다.

```c
uint8_t address = 0;
  while(HAL_I2C_IsDeviceReady(&hi2c1, address, 10, 1000)!=HAL_OK) {
      address++;
  }
  printf("I2C Address is 0x%02X(7bit value)\r\n", address>>1);
  while(1);
```

### ADC 배터리 잔량측정

sys > serial Wire (안하면 target is not responding retrying 오류 발생)

analog > adc1 > in1
Scan Conversion Mode: Disabled

Continuous Conversion Mode: Disabled

Discontinuous Conversion Mode: Disabled

External Trigger Conversion: Software Start

DMA Continuous Requests: Disabled

Data Alignment: Right

Number of Conversion: 1

channel : ADC1_IN1
Rank : 1
Sampling Time : 239.5 cycles (정확도 ↑)

connectivity > i2c1 > speed : 100kHz (표준속도)

> 참고링크 : https://blog.naver.com/kiatwins/221118252542<br>
> 참고링크 : https://www.micropeta.com/video57

---
#### 선형 보간 방식을 적용한 ADC 배터리 측정
## 코드 설명
동작 요약 : ADC 기능을 이용해 배터리 전압을 측정하고, 계산된 전압과 잔량 퍼센트를 I2C 방식의 LCD에 1초마다 출력한다.

### 1. ADC 전압출력 및 배터리 전압 → 퍼센트 계산 함수

#### 보정 계수 정의
```c
float correction = 3.15/3.11f;
```
- 멀티미터로 측정한 ADC 핀으로 입력되는 전압은 3.15v인 반면, ADC 출력은 3.11v이기 때문에 오차를 보정하기 위한 비례 계수를 적용

#### ADC 값 읽기
```c
HAL_ADC_Start(&hadc1);
HAL_ADC_PollForConversion(&hadc1, HAL_MAX_DELAY);
uint16_t adc_val = HAL_ADC_GetValue(&hadc1);
HAL_ADC_Stop(&hadc1);
```
- ADC 변환 시작 → 완료 대기 → ADC 값 읽기 → 변환 종료 순서

#### ADC 값 → 분압된 전압(Vout) 계산
```c
float vout_raw = (3.3f * adc_val) / 4095.0f;
float vout = vout_raw * correction;
```
- 12비트 ADC 기준 최대값은 4095이므로, 3.3V * (adc_val / 4095)로 ADC 핀의 실제 전압을 구하고 보정 계수로 실제 측정값에 더 근접한 값으로 보정

#### 분압 비율을 통해 실제 배터리 전압(Vbat) 계산
```c
float vbat = vout * ((19.7f + 6.73f) / 6.73f);  // ≈ 3.927
```
- 멀티미터 측정 기반 실제 저항 값 반영 후 저항 분압 회로의 비율에 따라 원래 배터리 전압을 복원
- Vout은 분압된 값이므로, 역으로 Vbat = Vout * (R1+R2)/R2

#### 전압 → 퍼센트로 환산, 범위제한
```c
float percent = ((vbat - 9.0f) / (12.6f - 9.0f)) * 100.0f;

if (percent > 100.0f) percent = 100.0f;
if (percent < 0.0f) percent = 0.0f;
```
- 배터리 전압이 9.0V~12.6V 범위일 때, 해당 전압이 몇 퍼센트에 해당하는지 계산
- 실제 전압이 범위를 벗어날 수 있으므로 출력값은 0~100%로 클램핑

### 2. main 함수

#### LCD 초기화
```c
HD44780_Init(2);   // 2줄 LCD 설정
HD44780_Clear();   // LCD 화면 초기화
```
- liquidcrystal_i2c.h 기반 라이브러리 사용하여 I2C LCD 모듈 초기화

#### 출력 문자열 변수 선언
```c
char line1[16], line2[16];
```
- LCD에 출력할 문자열 버퍼
- HD44780 LCD는 16x2 문자형 디스플레이이므로 16바이트 확보

#### 무한루프 내부 동작

##### 1. 배터리 상태 측정
```c
float vout = 0.0f;
float percent = Read_Battery_Percentage(&vout);
```
- Read_Battery_Percentage() 호출로
vout에 보정된 ADC 출력 전압 저장
- 반환값으로 percent에 배터리 잔량 계산

##### 2. 문자열 구성
```c
uint8_t display_percent = (uint8_t)(percent + 0.5f);
snprintf(line1, sizeof(line1), "Battery: %3d%%", display_percent);
snprintf(line2, sizeof(line2), "Voltage: %.2f V", vout);
```
- percent를 반올림한 뒤 정수 형태로 출력
- line1: 잔량, line2: 전압

##### 3. LCD 출력
```c
HD44780_Clear(); //초기화
// 각 줄에 문자열 출력
HD44780_SetCursor(0, 0);
HD44780_PrintStr(line1);

HD44780_SetCursor(0, 1);
HD44780_PrintStr(line2);

// 매 1초마다 업데이트 주기 설정
HAL_Delay(1000); 
```

> 참고링크 : https://www.micropeta.com/video57 <br>

---

## 문제 해결 및 개선/확장

### 문제상황 1.
리튬배터리의 정상 사용범위는 12.6v ~ 9.6v이며, 배터리 보호 회로 BMS의 컷오프 전압은 보통 9.0V 근처이다. STM32의 외부전원과 dc모터 전원으로 함께 사용하기 때문에 9.6V 정도가 실질적인 사용 한계로 봐야 하며 그 이하로 떨어지면 출력이 급격히 약해짐<br>
**해결** : 이전 코드의 전압범위를 12.6v to 9.6v로 수정하여 해결하였다.

### 문제상황 2.
STM32CubeIDE (GCC toolchain 기반)에서 printf()는 기본적으로 float 포맷팅 (%f, %.2f 등)을 지원하지 않도록 설정되어 있음 <br>
→ 코드에는 문제 없지만 링커 설정이 부족해서 컴파일러가 지원하지 못함<br>
**해결** : 프로젝트 우클릭 > properties > c/c++ build -> settings > tool settings > mcu/mpu settings > use float printf, scanf 두 개 체크

---

## 향후 확장 및 개선 아이디어
- 룩업 테이블 + 선형 보간 방식 적용<br>
(비선형 전압-잔량 특성을 반영한 LUT 기반 방식
오차 줄이기 위해 전압→% 보간)

- 전압 히스테리시스 + 디지털 필터 <br>
(ADC 입력값 평균 필터링 적용 → 노이즈 대응
급격한 전압 하락에 대해 히스테리시스 적용해 잔량 출력 안정화)

- ADC 내부 채널을 활용한 칩 내부 온도센서 값 디스플레이
-> https://blog.naver.com/leeinje66/223139324543

- LED low battery 경고 등 추가 및 9.6v 이하에서는 모터 동작 강제 중단 기능 고려

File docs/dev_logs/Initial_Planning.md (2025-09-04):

# 프로젝트 초기 계획

## 프로젝트 명 : 핸들링 모션 기반 RC카 네트워크 시스템

## 아이디어 도출과정 및 프로젝트 목표

현재 RC카 시장의 조종기는 대부분 조이스틱 혹은 건(Gun) 타입이며, 이는 실제 차량의 스티어링 휠 기반 조작 방식과 큰 차이를 보인다. 동시에, 실제 자동차 산업에서는 CAN(Controller Area Network) 통신이 차량 내 전자 장치 간의 데이터 교환을 위한 표준 네트워크로 자리 잡았으나, 취미용 RC카 분야에서는 이러한 전문적인 네트워크 기술이 거의 적용되지 않고 있다.

기존 RC카의 비직관적인 조종 방식에 아쉬움을 느꼈고, 실제 운전과 같은 실감 나는 경험을 제공하고 싶다는 생각을 갖게 되었다. 또한, 단순한 RC카 시스템을 만드는 것을 넘어, 실제 자동차 산업 현장에서 사용되는 CAN 통신과 RTOS(실시간 운영체제) 기술을 직접 적용하며 완성도 높은 임베디드 시스템을 RC카에 구현하고 싶었다.

이를 위해 다음과 같은 핵심 목표를 설정하였다.

- `직관적인 모션 컨트롤러 구현` : 실제 핸들링 모션을 IMU 센서로 정밀하게 수집 및 처리하고, 안정적인 RF 통신을 통해 RC카에 실시간으로 조향 명령을 전달한다.

- `CAN 기반 분산 제어 시스템 구축` : 차량의 제어부를 기능별 노드(ECU)로 분리하고 이를 CAN 통신으로 연결하여, 데이터 수집 및 명령 전달이 가능한 통합 네트워크 시스템을 구현한다.

- `양방향 원격 측정(Telemetry) 기능 구현` : 컨트롤러와 차량 간 양방향 무선 통신 네트워크를 구성하여, 차량의 센서 데이터(충돌 경고 신호, 속력 등)를 컨트롤러로 실시간 전송하고 사용자에게 피드백한다.

- `FreeRTOS 기반 멀티태스킹 시스템 구현` : 컨트롤러와 차량의 모든 제어기에 FreeRTOS를 적용하여, 센서 처리, 통신, 모터 제어 등 여러 작업을 안정적으로 동시에 처리하는 멀티태스킹 시스템을 구현한다.

- `합리적인 부품 구성을 통한 가격 경쟁력 확보` : 고가의 상용 부품 대신 널리 사용되는 가성비 모듈(STM32F103, nRF24L01 등)을 채택하여, 낮은 생산 단가로도 전문적인 제어 시스템을 구현할 수 있음을 증명한다.

본 작품은 단순한 RC카를 넘어, 미래 자동차 기술의 핵심 요소인 직관적 인터페이스, 차량 내 네트워크, 실시간 데이터 처리 기술을 소형 모델에 집약적으로 구현한다. 이는 취미 분야에 전문적인 제어 방식과 높은 수준의 현실감을 제공할 뿐만 아니라, 산업용 원격 제어 로봇이나 농기계 등 다양한 원격 제어 시스템에 적용 가능한 프로토타입으로서의 가치를 가질 것으로 예상된다.

---

## 보드 및 부품 선정

본 프로젝트의 모든 제어 유닛(컨트롤러 1개, 차량 내부 3개)의 MCU는 STM32F103C8T6로 통일하여 개발 환경의 일관성과 효율성을 확보하였다.

STM32F103C8T6는 ARM Cortex-M3 코어를 기반으로 72MHz의 충분한 클럭 속도를 제공하여 각 노드의 요구사항을 안정적으로 처리할 수 있다. 컨트롤러에서는 IMU 센서 데이터 처리 및 RF 통신을 담당하고, 차량 내에서는 메인 제어, 센서 데이터 처리, 모터 구동 등 각자 분담된 역할을 수행한다. 
특히 하드웨어적으로 CAN 컨트롤러를 내장하고 있어 별도의 컨트롤러 없이 CAN 트랜시버 모듈(MCP2551)만으로 안정적인 차량 내 네트워크를 구성할 수 있다. 또한 FreeRTOS를 구동하기에 충분한 성능을 갖추고 있으면서도 가격 경쟁력이 뛰어나, 본 프로젝트의 분산 제어 시스템 컨셉에 가장 적합한 MCU이다.

< 컨트롤러 (조종기) 부 >
- MCU: STM32F103C8T6
- 모션 센서: MPU6050 (6축 IMU 센서)
- 무선 통신: nRF24L01 (2.4GHz RF 송수신 모듈)
- 사용자 입력: 푸시 버튼 (엑셀/브레이크), 토글 스위치 (전/후진)
- 사용자 피드백: 햅틱 모터 (차량 상태 피드백)
- 디스플레이: SSD1306 (1.3인치 OLED)
- 18650 리튬 배터리(2s)

< 차량 부 (RC카) >
- 차량 섀시 키트
- MCU: STM32F103C8T6 (메인 제어부, 센서부, 디스플레이부 - 총 3개 사용)
- 무선 통신: nRF24L01 (2.4GHz RF 송수신 모듈)
- CAN 통신: MCP2551 (CAN 트랜시버 모듈)
- DC모터 : JGA25-370
- 모터 드라이버: L298N
- 서보모터 : MG996R
- 초음파 센서: HC-SR04
- 조도 센서 : LM393 ldr
- 기타: LED, 18650 리튬 배터리(3s), XL4015 DC-DC 스텝다운 컨버터, 저항, 로커 스위치

> [자세한 부품 사항](../parts_list.md)

---

## 마일드스톤 개괄 (약 3~4개월 예상)
- 1주~4주차 : 아이디어 구상 및 각 기능 모듈화
- 5주~8주차 : 통신 프로토콜 작성 및 구현
- 9주~12주차 : 각 모듈 RTOS 기반 태스크 스케줄링
- 13주~15주차 : 차량 및 컨트롤러 하드웨어 어셈블 후 시연

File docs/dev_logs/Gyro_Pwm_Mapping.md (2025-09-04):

# [I2C OLED] 자이로센서 Roll 값 실시간 디스플레이

## 프로젝트 활용 방안
본 프로젝트는 RC카의 핸들 제어용 무선 컨트롤러에 자이로센서(MPU6050)를 탑재하여,
사용자의 손목 회전(Roll 각도)을 감지하고 이를 실시간으로 I2C 기반 OLED(SSD1306)에
시각적으로 표시하는 기능을 구현한다. 이를 통해 사용자는 조향 입력의 반응을 직관적으로
확인할 수 있으며, 센서 데이터 수신 및 시스템 동작 상태를 검증할 수 있다.

---

## 이론 개요
### Roll 각도 → 서보모터 PWM 신호 매핑 원리

자이로센서에서 측정된 Roll 각도는 -90도에서 +90도 사이의 값이며, 이 각도를 서보모터 제어에 필요한 PWM 신호로 선형적으로 변환한다.

#### 변환 흐름:

1. **Roll 범위 조정**  
   - 센서 값: `-90.0° ~ +90.0°`  
   - 기준점 0으로 변환: `angle = roll + 90.0` → `0° ~ 180°`

2. **PWM 신호로 매핑**  
   - 서보모터 제어 범위: `330 ~ 730` (TIM2 PWM 기준)  
   - 수식:  
     \[
     pwm = 330 + \left(\frac{angle}{180.0}\right) \times 400
     \]
   - 즉, 0도일 때 330, 180도일 때 730으로 선형 증가

3. **타이머에 적용**  
   - HAL 라이브러리 함수로 PWM 출력값 반영:  
     ```c
     __HAL_TIM_SET_COMPARE(&htim2, TIM_CHANNEL_3, pwm);
     ```

#### 시각화 예시:

| Roll(°) |  PWM 값 |
|---|---|
| -90 |330 |
| 0 |530 |
| +90 |730 |

> 기울어진 방향에 따라 서보모터가 정비례적으로 회전하게 만들며, 직관적인 제어에 유리하다.

---

## 코드 설명: Roll → PWM 매핑

MPU6050에서 계산된 Roll 각도(`-90° ~ +90°`)를 기준으로 서보모터가 회전하도록 하기 위해, 이 각도를 TIM2의 PWM 신호 범위(`330 ~ 730`)로 선형 매핑한다. 이후 해당 PWM 값을 비교 레지스터에 설정하여 서보모터의 듀티비를 실시간으로 변경한다.

```c
// 자이로센서로부터 roll 각도 가져오기
float roll = MPU6050.KalmanAngleX;

// 예외 상황 대비: 센서 오차나 진동으로 인한 극단값 제거
if (roll < -90.0f) roll = -90.0f;
if (roll > 90.0f)  roll = 90.0f;

// 기준점 조정: -90 ~ +90 → 0 ~ 180 으로 변환
float angle = roll + 90.0f;

// angle(0~180)을 서보모터용 PWM 범위(330~730)로 선형 매핑
uint16_t pwm = (uint16_t)(330 + (angle / 180.0f) * 400.0f);

// 매핑된 PWM 값을 TIM2의 채널 3에 설정 (실제 서보모터 제어 신호로 출력)
__HAL_TIM_SET_COMPARE(&htim2, TIM_CHANNEL_3, pwm);
```

---

### 세부 설명

| 단계 | 설명 |
|---|---|
| **Roll 값 수신** | `MPU6050.KalmanAngleX`는 칼만 필터를 적용한 안정된 Roll 각도 값 |
| **클램핑** | ±90도를 넘는 센서 노이즈를 방지하고 서보모터 과도 동작 방지 목적 |
| **선형 매핑** | `roll + 90`으로 기준점을 0으로 설정한 후, 전체 180도를 기준으로 `330~730` 범위에 대응되도록 선형 변환 |
| **PWM 설정** | STM32의 `__HAL_TIM_SET_COMPARE()` 함수는 TIM2 채널 3의 CCR 레지스터 값을 갱신하며, 이 값은 PWM 듀티비를 결정| 

---

## 향후 확장 방향

- M4 보드의 고속 클럭 기반 높은 해상도의 PWM 듀티비 매핑
- 무선 송신(NRF24L01) 연동
- FreeRTOS 기반 태스크 분리
---

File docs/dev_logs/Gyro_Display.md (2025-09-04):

# [I2C OLED] 자이로센서 Roll 값 실시간 디스플레이

## 프로젝트 활용 방안
본 프로젝트는 RC카 핸들 제어를 위한 무선 컨트롤러에 자이로센서(MPU6050)를 장착하고, 차량의 회전 상태(Roll 각도)를 실시간으로 I2C 방식 OLED(SSD1306)에 시각적으로 출력하는 기능을 구현한다. 운전자의 직관적인 제어를 돕고, 자이로센서 데이터가 정상적으로 수신되고 있는지를 현장에서 즉시 확인하는 데 활용할 수 있다.

---

## 이론 개요

### MPU6050 자이로센서 동작 원리
MPU6050은 3축 가속도계와 3축 자이로스코프가 통합된 6축 센서로, I2C 인터페이스를 통해 데이터를 송수신한다. 내부에 칼만 필터(Kalman filter)가 적용된 연산을 통해 자세(Roll, Pitch)를 비교적 안정적으로 계산할 수 있으며, 본 프로젝트에서는 Roll 각도만 추출하여 OLED에 출력한다.

### SSD1306 OLED 디스플레이 동작 원리
SSD1306은 128x64 해상도의 모노크롬 OLED 디스플레이로, SPI 또는 I2C로 MCU와 통신한다. 본 프로젝트에서는 I2C를 채택하여 데이터와 명령어를 전송하고, 그래픽 라이브러리(`fonts.h`, `ssd1306.h`)를 통해 텍스트를 출력한다.

---

## 하드웨어 연결

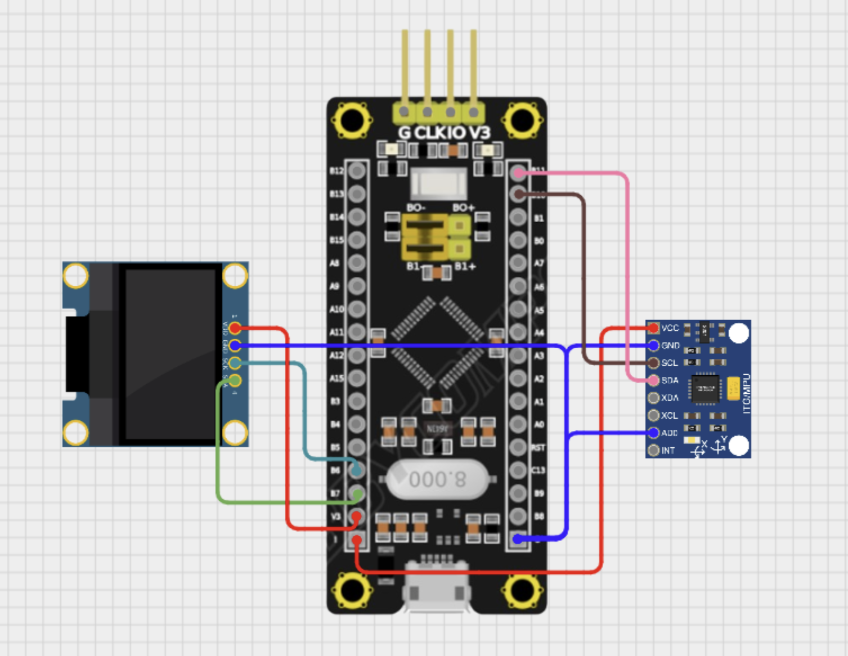
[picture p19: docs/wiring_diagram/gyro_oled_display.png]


### 자이로센서(MPU6050) 연결

|센서 핀|STM32F103C8T6 핀|
|:---:|:---:|
|Vcc|3.3V|
|GND|GND|
|SDA|PB11 (I2C2_SDA)|
|SCL|PB10 (I2C2_SCL)|

---

### OLED(SSD1306) 연결

|OLED 핀|STM32F103C8T6 핀|
|:---:|:---:|
|Vcc|3.3V|
|GND|GND|
|SDA|PB7 (I2C1_SDA)|
|SCL|PB6 (I2C1_SCL)|

- MPU6050과 OLED는 각각 I2C2, I2C1에 분리 연결

---

## STM32CubeMX 설정

### I2C
- `I2C1(OLED)` : Speed mode = 400kHz
- `I2C2(Gyro)` : Speed mode = 400kHz

### SYS
- Debug: Serial Wire 설정

### 기타
- OLED 라이브러리:  
 `fonts.h`, `ssd1306.h` -> Inc
 `fonts.c`,`ssd1306.c` -> Src

- MPU6050 라이브러리:   
`mpu6050.h` -> Inc  
`mpu6050.c` -> Src

> github 라이브러리 출처: https://github.com/leech001/MPU6050?tab=readme-ov-file
---

## 코드 설명

동작 요약: I2C2를 통해 MPU6050의 roll 값을 읽고, I2C1을 통해 SSD1306 OLED에 1초 주기로 출력한다.

### main 루틴 핵심

```c
while (1)
{
    // 자이로센서 데이터 갱신
    MPU6050_Read_All(&hi2c2, &MPU6050);

    // Roll 각도 출력
    char buffer_roll[20];
    snprintf(buffer_roll, sizeof(buffer_roll), "Roll: %.2f", MPU6050.KalmanAngleX);
    SSD1306_GotoXY(0, 0);
    SSD1306_Puts(buffer_roll, &Font_11x18, 1);

    // 디스플레이 반영
    SSD1306_UpdateScreen();
    HAL_Delay(100);
}
```

## 자이로센서 원시 데이터와 절대 각도 추정의 한계

### 자이로센서 원시 데이터란?

MPU6050 자이로센서는 3축의 회전 속도(각속도)를 측정하며, 그 값은 다음과 같은 변수로 저장된다:

- `Gyro_X_RAW`, `Gyro_Y_RAW`, `Gyro_Z_RAW`  
  → 각각 X, Y, Z 축의 **각속도(angular velocity)** 를 나타내며 단위는 일반적으로 **도/초 (deg/s)** 또는 **라디안/초 (rad/s)** 이다.

예를 들어:

```c
Gx = Gyro_X_RAW / 131.0;  // FS_SEL = 0 설정 기준, 1 LSB = 131 deg/s
```

- 이 값은 **회전한 정도(각도)**가 아니라 **회전의 속도**, 즉 “얼마나 빠르게 회전하고 있는가”를 의미한다.

---

### 자이로센서는 절대 각도를 직접 측정할 수 없다

- 자이로센서는 오직 **회전 속도의 변화량(각속도)** 만을 측정할 수 있다.
- 따라서 현재의 **절대 기울기(Roll, Pitch, Yaw)** 를 직접적으로 알 수 없다.

#### 누적 적분 방식의 한계

각속도를 시간에 따라 적분하여 회전 각도를 유추할 수는 있으나, 다음과 같은 문제가 존재한다:

| 문제 | 설명 |
|---|---|
| **드리프트(Drift)** | 아주 작은 오차도 시간이 지남에 따라 누적되어 심각한 각도 오차를 유발 |
| **초기 기준값 없음** | 절대 각도를 제공하지 않기 때문에 시작 각도가 불명확함 |

---

### 절대 각도 추정을 위한 센서 융합: 칼만 필터의 역할

이를 해결하기 위해 **가속도계 + 자이로센서**를 융합하고, **칼만 필터(Kalman Filter)** 를 적용하여 보다 정확한 절대 자세(Roll, Pitch)를 계산한다.

#### 가속도계 vs 자이로센서

| 센서 | 특징 | 장점 | 단점 |
|---|---|---|---|
| 가속도계 | 중력 방향 기준으로 기울기 계산 | 정적 상태에서 정확 | 움직임에 매우 민감 |
| 자이로센서 | 각속도 측정 | 움직임 추적에 강함 | 시간이 지날수록 오차 누적 |

#### 칼만 필터는?

- 두 센서의 장점을 융합하여 절대 각도를 실시간으로 추정
- 자이로센서의 빠른 반응성과 가속도계의 절대 기준 값을 조합
- 오차 공분산 행렬과 예측/보정 단계를 반복하며 최적의 상태 추정 수행

> 본 프로젝트에서는 roll 각도(`KalmanAngleX`) 계산 시, 칼만 필터를 통해 자이로센서 기반 누적값을 보정하고 있다.

---

### Roll 각도 계산 과정

MPU6050의 가속도계와 자이로스코프에서 읽은 원시 데이터를 기반으로, roll 각도를 계산하는 과정은 다음과 같다:

#### 1. 가속도계 기반 roll 각도 추정 (비선형 모델)

```c
double roll_sqrt = sqrt(Accel_X_RAW^2 + Accel_Z_RAW^2);
double roll = atan(Accel_Y_RAW / roll_sqrt) * RAD_TO_DEG;
```

- 수직 방향으로 중력 가속도를 기준으로, Y축의 기울기를 X축-Z축 평면 기준으로 아크탄젠트 연산
- `RAD_TO_DEG`는 라디안을 도(degree)로 변환하는 상수 (≈ 57.2958)

이 방식은 고정된 상태에선 정확하나 움직임이나 진동, 외란이 있을 경우 불안정함

#### 2. 자이로스코프 기반 회전 속도 추정

```c
Gx = Gyro_X_RAW / 131.0;
```

- MPU6050 자이로스코프의 출력은 16비트 정수로 되어 있으며, `FS_SEL = 0` 설정 시 1 LSB는 131 deg/sec에 해당
- 자이로는 순간적인 회전 속도를 측정하지만, 이를 시간 적분하여 각도로 변환하면 누적 오차가 발생

#### 3. 칼만 필터 기반 roll 추정

```c
KalmanAngleX = Kalman_getAngle(&KalmanX, roll, Gx, dt);
```

- 가속도계에서 계산한 `roll`과 자이로스코프의 회전속도 `Gx`를 칼만 필터에 입력
- 이전 상태를 기반으로 현재 상태를 추정하고, 두 센서의 장점을 결합하여 더 안정적인 roll 추정

---

### Kalman Filter 내부 작동 방식

칼만 필터는 다음과 같은 수학적 절차로 구성된다:

#### 상태 변수
- `angle`: 추정 각도
- `bias`: 자이로스코프 바이어스 오차 추정
- `P[2][2]`: 오차 공분산 행렬

#### 주요 수식

```c
rate = newRate - bias;
angle += dt * rate;

P 업데이트...

K[0] = P[0][0] / S;
K[1] = P[1][0] / S;

angle += K[0] * (newAngle - angle);
bias  += K[1] * (newAngle - angle);

P 행렬 보정...
```

- **예측 단계 (Prediction)**: 자이로 데이터를 시간에 따라 누적하여 새로운 각도 예측
- **보정 단계 (Correction)**: 가속도계를 통해 측정한 각도와의 오차를 기반으로 예측값을 보정
- 오차 공분산 행렬 `P`를 갱신하면서 신뢰도에 따라 두 센서의 가중치를 자동 조절

---

### 정리

| 센서 | 장점 | 단점 |
|---|---|---|
| 가속도계 | 절대 각도 기반 측정 가능 (중력 기준) | 노이즈에 민감, 동작 중 정확도 낮음 |
| 자이로스코프 | 빠른 동작에 강함, 순간 변화 민감 | 시간에 따라 드리프트(누적 오차) 발생 |
| 칼만 필터 | 두 센서의 장점을 결합하여 실시간 자세 추정 | 계산량이 많음, 구현 복잡도 ↑ |

---

### 관련 구조체 및 초기값

```c
Kalman_t KalmanX = {
    .Q_angle = 0.001f,
    .Q_bias = 0.003f,
    .R_measure = 0.03f
};
```

- `Q_angle`: 각도에 대한 프로세스 노이즈 공분산
- `Q_bias`: 바이어스 노이즈 공분산
- `R_measure`: 측정 노이즈 공분산
- 값이 작을수록 필터가 측정치보다는 예측치에 더 의존

> 칼만 필터 알고리즘 참고: https://github.com/TKJElectronics/KalmanFilter  
> 본 코드 기반: `mpu6050.c` (Author: Bulanov Konstantin, 2019)

---

## 향후 확장 및 개선 아이디어

- **Yaw/Pitch 각도 병행 출력**  
  → Roll 외에도 Pitch 및 Yaw 각도를 함께 출력하여 3축 자세 정보 제공

- **UI 향상**  
  → Roll 값 기반 그래픽 표시(수평 막대, 방향 화살표 등) 적용하여 시인성 향상

- **무선 전송 연동**  
  → Roll 값을 NRF24L01 무선 송신 기능과 연동하여 차량 제어 MCU로 전송

- **FreeRTOS 적용**  
  → 센서 수집, OLED 출력, 무선 전송을 Task로 분리하여 안정적인 실시간 제어 구조 구축

- **센서 보정 기능 추가**  
  → Roll 값의 기준점(제로 레벨)을 전원 인가 시 또는 버튼 입력 시 기준으로 재설정

---

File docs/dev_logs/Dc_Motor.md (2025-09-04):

# [JGA25-370] PWM 듀티비 기반 DC모터 동작 로직 구현

## 프로젝트 활용 방안
본 프로젝트에서 DC 모터는 차량의 후륜 구동을 담당하며, 모터에 부착된 인코더를 통해 속도(RPM)를 측정하며, 모터 드라이버를 통해 회전 방향(전진/후진)을 제어한다. RPM은 sensor부에서 담당하며, 이는 추후 컨트롤러부의 OLED에서 디스플레이할 예정이다.

---

## 이론 개요

### 1. JGA25-370 DC모터 with 인코더 동작 원리

#### 모터 사양
- Rated Volt : 12v
- Reduction ratio : 21.3:1
- No Load(무부하)
    - speed : 280rpm<br>
	- current : 60mA<br>
- At Load(부하)
    - Torque : 0.5KG.cm
	- speed : 220rpm
	- current : 0.45A
- Stall 
    - TOGQCE : 1.7KG..CM
	- current : 1.3A

#### DC모터 동작원리
- JGA25-370과 같은 브러시드 DC 모터는 입력 전압의 크기에 따라 회전 속도가 변하는 구조를 가지며, 이를 효율적으로 제어하기 위해 일반적으로 PWM(Pulse Width Modulation, 펄스 폭 변조) 방식이 사용된다.
- PWM 방식은 전압을 아날로그처럼 연속적으로 제어하는 대신, 디지털 신호의 ON/OFF 시간을 조절함으로써 모터에 **전력 공급의 평균값(평균 전압)**을 바꾸는 방식이다. 
    - 예를 들어, 100% 듀티 비는 전압이 계속 공급되는 상태(12V), 50% 듀티 비는 절반 시간만 공급되어 평균 약 6V, 10% 듀티 비는 약 1.2V의 평균 전압 효과를 내게 된다. 이에 따라 모터의 속도도 비례적으로 달라지게 된다.

- 다만, JGA25-370은 감속 기어가 포함된 고토크 저속 모터이기 때문에, 회전 시작 시 관성이 커서 일정 이상의 전압이 인가되어야 실제로 회전을 시작할 수 있다. 일반적으로 듀티 비 20~25% 이하에서는 모터가 회전하지 않고 데드존(Dead Zone) 현상이 발생해 소음만 존재하며, 실제 속도 제어가 되지 않는다. 따라서 유효한 제어 범위는 이 이상에서 시작된다.

- 하지만 너무 빠른 PWM 주파수는 감속기의 반응 속도나 모터의 기계적 특성 때문에 각 펄스의 세부적인 전력 변화에 모터가 민감하게 반응하지 못해, 오히려 제어 해상도가 떨어질 수 있다. 특히 JGA25-370과 같이 감속기가 포함된 고관성 모터는 회전 반응이 느리기 때문에 고주파 PWM의 빠른 듀티비 변화는 기계적으로 무시되거나 평균값으로만 반영되는 경우가 많다.
- 따라서 PWM 주파수는 모터가 실제로 반응할 수 있는 범위 내에서 설정하는 것이 중요하다. 일반적으로 브러시드 DC 모터의 경우 1kHz~20kHz 사이에서 동작하며, 너무 낮은 주파수는 출력이 끊기는 듯한 느낌을 줄 수 있고, 너무 높은 주파수는 실제 제어 효과가 무뎌지므로, 실험적으로 모터의 회전 반응성과 소음 수준을 고려해 최적 주파수를 선정해야 한다.

#### 홀 센서 방식의 회전 인코더
- JGA25-370 DC 모터에 장착된 인코더는 홀 센서 방식의 회전 인코더로, 회전축에 부착된 자석과 이를 감지하는 두 개의 고정된 홀 센서를 이용해 회전 속도와 방향을 측정한다. 회전 시 자석의 자기장 변화에 따라 홀 센서가 홀 전압을 발생시키고 이를 디지털 펄스로 변환하여 출력하며, 두 센서(A상, B상) 간의 위상차를 분석함으로써 회전 방향을 판단할 수 있다. 생성된 펄스 수를 시간에 따라 카운트하면 회전 속도(RPM)를 계산할 수 있다. 
- 홀 센서 방식은 해상도 면에서는 광학식보다 낮지만, 먼지, 진동, 오염에 강해 내구성이 뛰어나며, 산업용 및 차량용 모터 제어 시스템에 널리 사용된다.

##### 인코더 기본 구성
- 자석(Magnet): 모터 축에 부착되어 회전함
- 홀 센서(Hall Sensor): 자석의 N/S극 변화에 따른 자기장 변화를 감지하여 디지털 펄스를 출력

##### 인코더의 속도 측정 원리
1. 모터 회전 시, 자석이 홀 센서를 통과할 때마다 펄스 1개가 발생함
2. 일정 시간 동안 발생한 펄스 수를 세어 회전수를 계산함
3. 이를 바탕으로 회전속도(RPM)를 계산:
```text
RPM = (펄스 수 / TICKS_PER_REV) × (1초 / 측정 주기) × 60
```
- TICKS_PER_REV: 감속기 포함 실제 출력축 한 바퀴당 펄스 수
- STM32에서는 타이머 인터럽트나 주기 타이머를 통해 펄스 카운트를 주기적으로 측정함

##### 인코더의 방향 측정 원리 (쿼드러쳐(Quadrature) 기법)
   
|A상 신호|B상 신호|변화 순서|방향|
|:---:|:---:|:---:|:---:|
|↑|→|A상 상승 -> B상 상승|정방향 (CW)|
|→|↑|B상 상승 -> A상 상승|역방향 (CCW)|
- 회전 인코더에서 두 개의 홀 센서 신호 A상과 B상이 90도 위상차를 가지고 변화하면서, 신호 변화 순서에 따라 회전 방향을 측정할 수 있음

- 이 두 신호를 사용하면 펄스당 4번의 카운팅 (A 상승, A 하강, B 상승, B 하강)이 가능해져 4배 해상도의 정밀한 카운팅이 됨 **(x4 모드)**

- STM32의 Encoder 인터페이스 모드에서는 이 위상차를 자동으로 감지해 카운터 증가/감소로 방향을 판단

### 2. L298N 모터 드라이버 원리 (H-Bridge 방식)
L298N은 STMicroelectronics에서 제작한 듀얼 H-Bridge 모터 드라이버로, DC 모터나 스테퍼 모터를 양방향 제어하기 위해 설계되었다. 내부에는 두 개의 BJT 기반 H-Bridge 회로가 내장되어 있어, 하나의 L298N 칩으로 DC 모터 2개 혹은 스테퍼 모터 1개를 제어할 수 있다.

#### H-Bridge 기본 이론
H-Bridge 회로는 4개의 스위칭 소자(트랜지스터 또는 MOSFET)를 "H"자 형태로 배치하여, 전류의 방향을 양쪽으로 바꿀 수 있는 구조이다.

- 전류 방향 전환: 특정한 두 개의 스위치를 동시에 켜면 모터의 한 방향으로 전류가 흐르고, 다른 쌍을 켜면 반대 방향으로 흐름 → 모터 회전 방향 제어 가능

- PWM 제어: 상단 또는 하단의 트랜지스터 쌍에 PWM 신호를 입력하면, 전력의 평균값을 조절해 속도 제어가 가능함

#### PWM 주파수와 관련된 특성
L298N은 일반적으로 2kHz ~ 5kHz 사이의 PWM 주파수에서 안정적으로 동작하며, 이 범위를 벗어나면 다음과 같은 문제가 발생할 수 있다:

- 1kHz 이하의 저주파 : 모터 진동, 고주파 소음, 부드럽지 못한 회전 
- 10~20kHz의 고주파 : BJT의 스위칭 손실 증가 → L298N 발열 심화
출력 토크 감소, 효율 저하

※  Datasheet에서도 PWM 주파수에 대한 명시적인 권장치는 없지만, BJT 기반 스위칭 소자의 스펙과 실제 실험 결과를 보면 2~5kHz가 최적 동작 범위로 평가됨.

#### 왜 L298N은 고속 PWM에 적합하지 않은가?
- 스위칭 손실 증가: BJT는 MOSFET보다 on/off 시간이 느려, 빠른 PWM(예: 20kHz 이상)에서는 과도한 열 손실이 발생함

- 출력 저하: 빠른 스위칭 속도를 따라가지 못해 PWM 듀티비에 따른 출력 반응이 무뎌지고, 모터 토크가 줄어듦

- 발열 위험: 히트싱크 없이 사용 시, 고속 PWM + 고전류 조합은 **L298N 발열에 의한 열 차단(thermal shutdown)**을 유발할 수 있음

> [JGA25-370 datasheet](../datasheets/[JGA25-370]dc_motor_datasheet.pdf)<br>
> [L298N datasheet](../datasheets/[L298N]motor_driver_datasheet.pdf)<br>
> H-bridge 참고링크 : https://m.blog.naver.com/techref/222236636089<br>
> 인코더 참고링크 : https://blog.naver.com/gauya/220221704986
---

## 하드웨어 연결

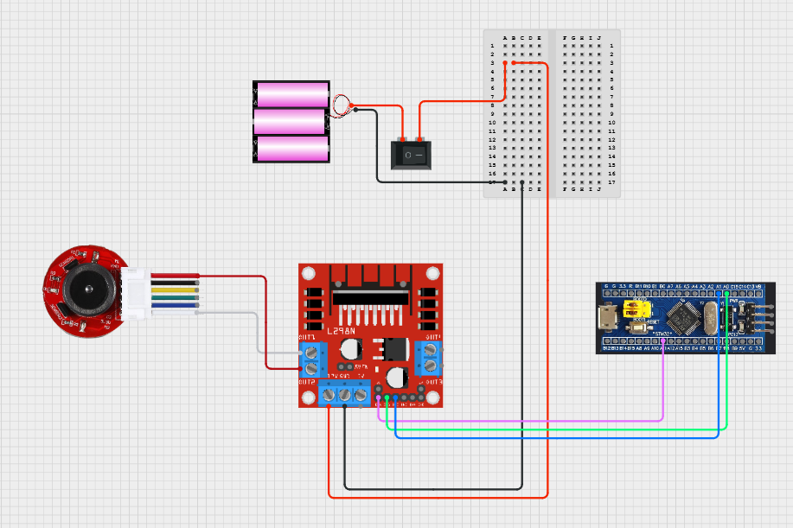
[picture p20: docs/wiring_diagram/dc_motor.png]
DC모터 결선도


|외부전원|L298N|F103보드|DC모터|
|:---:|:---:|:---:|:---:|
|+12V|+12v|||
|Gnd|Gnd|Gnd|-|
||Out1||Motor-(white)|
||Out2||Motor+(red)|
||IN1|PA0||
||IN2|PA1||
||ENA|PA11||

- 그라운드는 공통으로 묶어줘야함
- 점퍼핀 제거 후 ENA에 STM32의 PWM 핀(PA11)을 연결하면 모터 속도 제어가 가능하다. 
- ENA를 HIGH로 고정한 상태에서는 속도 조절 없이 ON/OFF 및 방향 제어만 된다.

---  

## STM32CubeMX 설정

## 1. Pinout 설정
- PA0, PA1 -> GPIO_Output (L298N IN1,2)
- PA11 -> TIM1_CH4 (PWM Generation)

### 2. TIM1 설정 - PWM
- Clock Source: Internal Clock
- Channel 3: PWM Generation CH4
- Configuration
    - Prescaler : 36-1 
    - Counter Period (ARR) : 1000-1

#### < TIM1의 타이머 클럭 계산 >
STM32F103C8T6에서 TIM1은 APB2 버스에 연결된 고성능 타이머이다. STM32F1 시리즈의 클럭 규칙에 따라 타이머의 동작 클럭이 결정된다.

- APB2 Prescaler = 1: 타이머 클럭 = APB2 클럭
- APB2 Prescaler > 1: 타이머 클럭 = APB2 클럭 × 2

일반적인 최대 클럭 설정에서 시스템 클럭(HCLK)과 APB2 클럭(PCLK2)은 모두 72MHz이며, APB2 Prescaler는 1로 설정된다. 따라서 TIM1에 공급되는 기본 타이머 클럭은 72MHz가 된다.

PWM 신호의 주기와 분해능을 결정하기 위해, 이 72MHz 클럭을 **Prescaler(PSC)**를 이용해 분주한다. 이 프로젝트에서는 **PSC 값을 35 (레지스터 설정값 36-1)**로 설정했다. 그 이유는 목표 PWM 주파수와 분해능을 고려했을 때, 타이머가 2MHz로 동작하는 것이 가장 이상적이기 때문이다.

- 타이머 카운팅 클럭 = 타이머 클럭 / (PSC + 1)
- 2MHz = 72MHz / (35 + 1)

따라서 PSC 값을 35로 설정하면, 타이머는 2MHz, 즉 0.5µs마다 한 번씩 카운트하게 된다.
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

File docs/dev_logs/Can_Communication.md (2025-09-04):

#  CAN 통신 송/수신 초기 기능 구현

## 프로젝트 활용 방안
CAN 통신은 본 프로젝트에서 다수의 마이크로컨트롤러 간 신뢰성 높은 데이터 교환을 위해 핵심적으로 활용된다. 현재 차량의 센서부에서 측정한 전·후방 초음파 센서 거리 데이터는, RF 통신을 통해 핸들부로 전송되기 전에 RF 송·수신 모듈이 탑재된 중앙제어부로 먼저 전달되어야 하며, 이 과정에서 CAN 통신이 사용된다. 또한 CAN의 브로드캐스트 특성을 활용하면, 향후 배터리 모니터링, 온도 센서 등 다양한 모듈을 추가하더라도 동일한 버스 상에서 통신 인프라를 확장성 있게 유지할 수 있다. 따라서 CAN 통신은 이 프로젝트에서 모듈 간의 분산제어 구조와 실시간 반응성을 확보하기 위한 필수 요소로 작용한다.

## 이론 개요
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

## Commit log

2025-05-22 develop 문서 파일 추가
2025-05-23 Update CubeIDE 토큰 관리법.md
2025-05-23 제목 변경
2025-05-25 초음파센서 연결도 폴더 추가
2025-05-26 OLED 회로도 업로드
2025-05-26 스위치 & LED 회로도 업로드
2025-05-27 ultrasonic_datasheet 추가
2025-05-27 2주차 초음파센서 개발일지 추가
2025-05-27 Update and rename ultrasonic.md to Ultrasonic.md
2025-05-27 주간 요약일지 추가
2025-05-27 Github with CubeIDE 정리 문서 dev_log로 이동
2025-05-29 배터리체크 with LCD 하드웨어 연결도 추가
2025-05-29 초음파센서 하드웨어 연결도 크기 수정
2025-05-29 초음파센서 하드웨어 연결도
2025-05-29 LCD 디스플레이 데이터시트 추가
2025-05-30 servo motor wiring diagram 추가
2025-06-01 ADC 기반 배터리 체크 LCD 모니터링 개발문서 추가
2025-06-01 자이로센서 & OLED 회로도 업로드
2025-06-02 서보모터 데이터시트 추가
2025-06-02 서보모터 개발문서 추가
2025-06-03 스위치 눌림 시간 측정 코드_Trouble_Shooting_수정
2025-06-05 디바운싱 스위치 회로도 업로드
2025-06-05 dc 모터 하드웨어 연결도 추가
2025-06-08 DC 모터 데이터시트 추가
2025-06-08 L298N 모터 드라이버 데이터시트 추가
2025-06-08 DC 모터 기술 문서 추가
    PWM + 엔코더 기반 DC모터 동작 및 RPM 측정 로직 구현
2025-06-09 main 함수의 while 루프의 중요성 업로드
2025-06-13 dc_motor_oled_switch 하드웨어 배선도 추가
2025-06-14 초음파센서 with 진동모터센서 배선도 추가
2025-06-14 초음파센서 배선도 수정
2025-06-15 Rename docs/datasheets/motors/Vibration Motor Module_datasheet.pdf to docs/datasheets/Vibration Motor Module_datasheet.pdf
2025-06-15 Rename Vibration Motor Module_datasheet.pdf to Vibration_Motor_Module_datasheet.pdf
2025-06-15 초음파센서기반 진동모터 동작 개발로그 추가
2025-06-16 DC모터 스위치 제어_OLED출력 개발로그 추가
2025-06-24 OLED 배터리 측정 배선도 추가
2025-06-24 ADC 배터리 측정 OLED 로직 변경사항 문서 추가
2025-06-24 스위치 기반 DC모터 전/후진 구동 및 OLED 출력 기술문서 수정
2025-07-02 m3 두 대 캔 통신 회로 구성도 추가
2025-07-09 Add files via upload
    RF 송/수신 기반 서보/DC모터 제어 통합 개발문서 추가
2025-07-09 RF 송수신 기반 모터제어 v1.0.0 개발문서 추가
2025-07-13 rf 통신 모듈 데이터시트 추가
2025-07-13 버튼눌림시간 acc,brk 및 자이로기반 서보조향 oled with RF통신 배선도 추가
2025-07-13 central_v1.0.0 배선도 추가
2025-07-13 Locker 스위치, Encoder 배선도 추가
2025-07-13 Locker 스위치 기반 전/후진 기능, Encoder 기반 RPM 측정 개발문서 추가
2025-07-15 00_WEEKLY_DEV_LOG_SUMMARY.md 업데이트
2025-07-17 Can 통신 개발일지 추가
2025-07-18 images 폴더 및 can tx,rx 이미지 추가
2025-07-22 can 통신 배선도 수정
2025-07-22 초음파-햅틱 CAN 통신 배선도 추가
2025-07-22 초음파센서-햅틱 CAN broadcast 방식 배선도 추가
2025-07-22 Broadcast 방식 기반 CAN 통신 (v1.5.0) 개발일지 추가
2025-07-24 컨트롤러 만능기판 업로드
2025-07-24 컨트롤러 만능기판 회로도 업로드
2025-07-29 status_v1.6.0 개발일지 추가
2025-08-05 컨트롤러부 RTOS 포팅 업로드
2025-08-05 버전 전환 시 유의점
2025-08-11 v1.7.0 dev_log 추가
2025-08-12 ldr,brk,dir기반 LED 배선도 추가
2025-08-14 모델링 파일 업로드
2025-09-01 stlink to f103 board connection error solved
2025-09-01 컨트롤러 만능기판 설계도
2025-09-01 can 트랜시버 모듈 사진 추가
2025-09-01 토글스위치 사진 추가
2025-09-01 저항 사진 추가
2025-09-01 docs: 프로젝트 문서정리
2025-09-02 central v2.0.0 개발일지 추가
2025-09-02 status부 v2.0.0 개발일지 추가
2025-09-02 sensor부 v2.0.0 개발일지추가
2025-09-02 컨트롤러 3D 모델링 개발일지 추가
2025-09-02 add controller 만능기판 설계도 추가
2025-09-02 저항 부품사진 추가
2025-09-04 컨트롤러부 v2.1.0 개발일지 추가
2025-09-04 dc모터 배선도 추가
2025-09-04 servo 모터 배선도 추가
2025-09-04 rpm 측정 배선도 추가
2025-09-04 토글스위치 모터방향 전환 배선도 추가
2025-09-04 RPM 측정 및 토글스위치 기반 전/후진 기어변속 개발일지 추가
2025-09-05 IMU 센서 오차보정 트러블슈팅 추가
2025-09-05 ACK_payload 기반 양방향통신 구현
2025-09-05 CAN 통신 확장성 문제 해결
